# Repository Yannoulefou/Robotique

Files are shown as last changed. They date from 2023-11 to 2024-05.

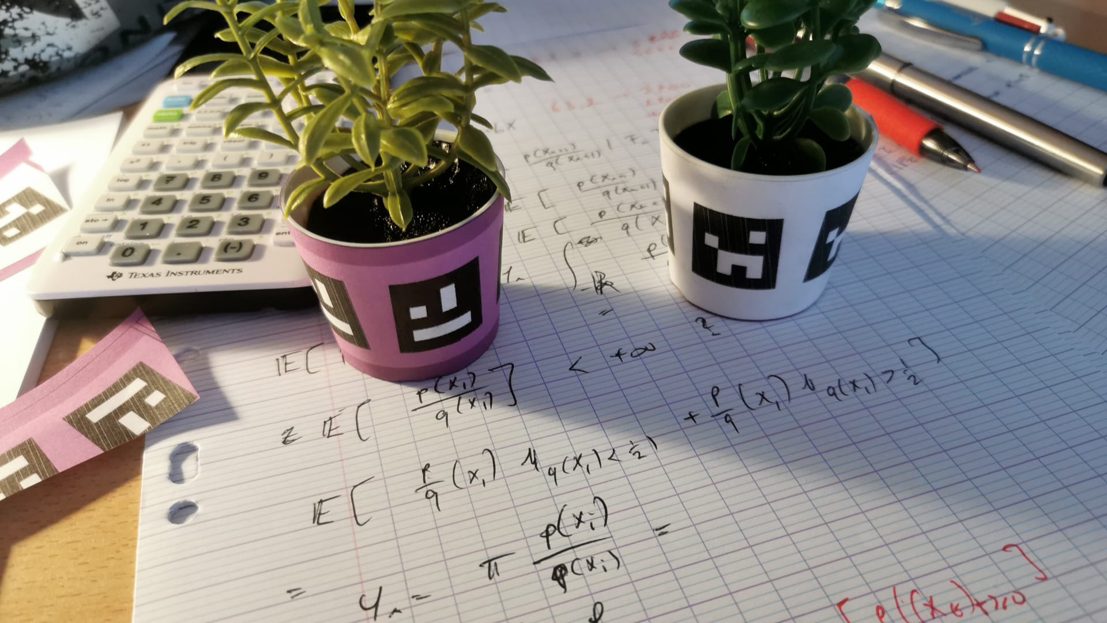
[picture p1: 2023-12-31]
Programmations/Tag Aruco/photo8.jpg

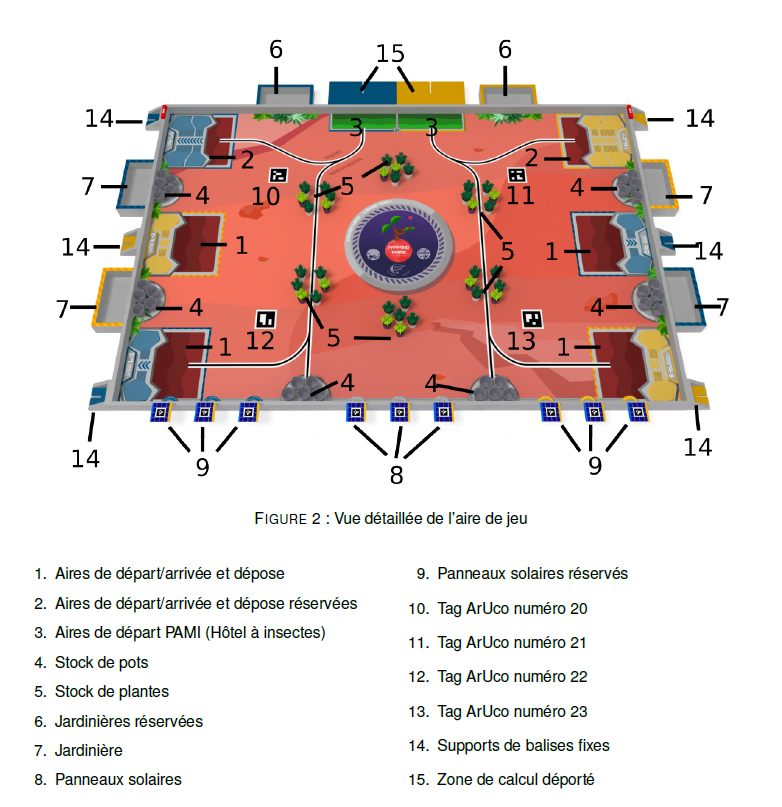
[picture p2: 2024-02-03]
Programmations/Moteur Deplacement/Schéma/Plateau.png

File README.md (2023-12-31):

# Robotique
Ce repo a pour but de centraliser tous les documents pour la participation à coupe de france de robotique 2023-2024 de TUXAE.  

## Sujet  
Farming Mars  
https://www.coupederobotique.fr/inscriptions-coupe-de-france-de-robotique-2024/  
https://www.eurobot.org/eurobot-contest/eurobot-2024/  

## Liens intéressants
https://github.com/VRAC-team/la-maxi-liste-ressources-eurobot  
https://github.com/LesKaribous   
https://howtomechatronics.com/projects/arduino-mecanum-wheels-robot/  
https://git.poivron-robotique.fr/Keuronde/Meca2024/src/branch/master   
https://mryslab.github.io/telemetrix/  

## Participants
### Conception Robot
 - Fanny DAUBET
 - Pierre DAUBET
 - Jacques ZHANG
 - Thomas CHEN
 - Tien-Thinh TRAN-THUONG (tttienthinh)

### Motorisation et roues omnidirectionnelles
 - Thomas ROUSSAUX

### Triangulation 
 - Victorien Marette  

### Caméra et computer Vision
 - Dasha HARYFULLINA ?

### Filtre de Kalman
 - Yassine BOUKHATEB (yassprogramme)
 - Mohamed KETEB
 - Guillot Paul (pyoph)

### Algorithme de décision (problème du sac à dos)
 - Wiam Lachqer ?
 - Bilal BENHANA ?
 - Rémy Siahaan-Gensollen ?

# Feuilles de route
## Novembre 2023
 - Apprendre à utiliser les machines (Imprimante 3D & Découpeuse Laser)
 - Réaliser des prototypes
 - Acheter les composants nécessaires
 - Lancer les différentes équipes

## Décembre 
 - Faire la demande de subvention pour l'association
 - Fixer un concept de robot
 - Réfléchir au cablage des composants et leur positionnement

## Janvier 2024
 - Commencer à intégrer les roues mecanum
 - Programmer le robot
 - Analyser l'algorithme de décision

## Février 
 - Commencer à intégrer la triangulation
 - Fabriquer les coccinelles
 - 10 février 2024 🏆 Rencontre Junior Auvergne-Rhône-Alpes 

## Mars
 - Commencer à intégrer les manoeuvres d'évitemment de l'adversaire
 - Commencer à intégrer une position plus précise par filtre de Kalman
 - 2 mars 2024 🏆 Rencontre Junior Ile-de-France 

## Avril 
 - 11 avril 2024 🏆 Eurobot Royaume-Uni 🇬🇧
 - 12 et 13 avril 2024 🏆 Eurobot et Eurobot Junior Espagne 🇪🇸
 - Rencontre à Télécom-Sud-Paris pour faire affronter les robots

## Mai
 - Du 8 au 11 mai 2024 🤖 Finales nationales et internationale 🤖

# Ressources

https://en.wikipedia.org/wiki/Python_Robotics  
https://arduinofactory.fr/pyfirmata/

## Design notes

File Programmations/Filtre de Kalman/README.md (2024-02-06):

# Les étapes
 - Comprendre le modèle 
 - Essayer de le mettre en place sur un modèle exemple : https://github.com/emmanuel-battesti/swarm-rescue/tree/main/src/swarm_rescue/examples
 - Essayer de comprendre les sources d'erreurs de la triangulation et les mesurer
 - Intégrer les erreurs pour l'estimation de la position

# Ressources
https://www.youtube.com/watch?v=IFeCIbljreY : Une vidéo très simple permettant de comprendre l'utilité du filtre de Kalman.

https://filterpy.readthedocs.io/en/latest/kalman/KalmanFilter.html : Un module python que j'ai déjà utilisé au sein d'un autre projet et que je trouve facile à prendre en main.

https://automaticaddison.com/extended-kalman-filter-ekf-with-python-code-example/ Une implémentation simple modèle #xt+1 = xt + v cos(theta)
#yt+1 = yt + v sin(theta) 
#theta_t+1 = theta_t + omega

https://atsushisakai.github.io/PythonRobotics/modules/slam/ekf_slam/ekf_slam.html#introduction Autre implémentation

https://github.com/rlabbe/Kalman-and-Bayesian-Filters-in-Python Des implémentations plus complexes ici

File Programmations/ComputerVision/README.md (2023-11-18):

# Les étapes
 - Lire un code barre dans une photo avec Python (1-lirecodebarre.py)
 - Essayer de dessiner soit même 3 code barres différents et les faire reconnaitre (1-lirecodebarre.py)
 - Identifier la position du Codebarre et son orientation (2-positioncodebarre.py)
 - Rendre la reconnaissance de code barre en temps réel et utiliser une caméra (3-webcam_live.py)
 - Faire en sorte que le temps réel ne prennent pas trop de ressources (3-webcam_live.py)
 - Basculer tout le code sur Raspberry avec la caméra intégré (4-Raspberry.py)
 - Faire la reconnaissance sur les poteaux de balises
 - Identifier la position de la balise et calculer la position en conséquence

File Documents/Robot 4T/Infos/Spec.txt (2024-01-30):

pyfirmata
https://github.com/MrYsLab/telemetrix
  
# Roue mecanum

Tbest Roue Omnidirectionnelle Mecan, Roue Omnidirectionnelle Mecanum en Alliage d'Aluminium de Robot RC avec Ecrous Dorés  
https://www.amazon.fr/Tbest-Omnidirectionnelle-Mecanum-Alliage-dAluminium/dp/B07YQJPFKW

Dimensions du produit (L x l x h) 	‎6 x 6 x 2,4 cm; 230 grammes 

Spécification:  
Condition: 100% tout neuf  
Type d'élément: Accessoire RC  
Matériau de la surface: alliage d'aluminium  
Couleur: comme sur les images  
Diamètre de roue: env.60mm/2.4in  
Modèle: 60mm  
Connecteur: env.12mm  
Roulement: 15 kg  
Épaisseur de roue: env.24mm  
Diamètre de l'essieu de la roue d'appui: env.4 mm  
Numéro de la roue de soutien: 10   

# Moteur NEMA

NEMA is an acronym for the National Electrical Manufacturers Association.  
NEMA 14 signifie que la face de devant fait 1.4*1.4 pouce = 3.5*3.5cm  
NEMA 17 signifie que la face de devant fait 1.7*1.7 pouce = 4.2*4.2cm  
La vitesse et le couple dépend donc de la longueur du moteur et de la puissance électrique acceptée.  

Différentes références de moteur NEMA :  
https://www.pololu.com/category/87/stepper-motors  

Exemple de NEMA 17
https://www.lextronic.fr/moteur-pas-a-pas-nema17-03-64826.html  

Sur omc-stepperonline.com   
Nema 23 série E bipolaire 1.8deg 1.26Nm 2.8A 57x57x56mm 4 fils €10.51    
Nema 17 Bipolaire 42Ncm  1.5A 42x42x38mm 4 Fils  €4.63  
Nema 17 Bipolaire 45Ncm 2A 42x42x40mm 4 Fils €7.69  
Nema 17 Bipolaire 59Ncm 2A 42x48mm 4 Fils €9.43   

# Moteur à encoder
333 rpm et 0.35 Nm  
https://www.lextronic.fr/motoreducteur-e52037gm-120333-76706.html  

# Batterie
[Comment alimenter la Raspberry](https://www.magdiblog.fr/divers/comment-alimenter-votre-raspberry-pi-avec-une-batterie/)  
Lipo : best mais dangeureuse lors de la charge  
Li ion : comme téléphone mais un peu chère  
Nimh (aka pile rechargeable) : Ok mais perd de puissance au cours de l'utilisation  

## melasta Li-ION Batterie Externe 5200mAh 12V/5A/DC 9V/1.5A/DC 5V/2A USB  
46,99€  
https://www.amazon.fr/Batterie-Portable-Compatible-Smartphone-Surveillance/dp/B0BRRR3C41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  
Power Bank Chargeur Portable avec Chargeur avec 3 Ports Sortie et 1 Entrées
Avec buton power off  

## Batterie Externe Power Bank 6000mAh 14.6V/5A/DC 9V/1.5A/DC 5V/2A USB   LiFePO4 
64,99€
https://www.amazon.fr/Batterie-Powerbank-Compatible-Smartphone-Surveillance/dp/B0BRTK7ZSD?ref_=ast_sto_dp  
Batterie Portable avec Chargeur avec 3 Ports USB Sortie et 1 Entrées  
Avec buton power off  

## Charmast 20000mAh 100W PD Batterie Externe Ordinateur Portable en USB C Batterie Portable Power Bank Quick Charge 3.0 
52,99€  
https://www.amazon.fr/Charmast-Ordinateur-Compatible-T%C3%A9l%C3%A9phone-Tablettes/dp/B0C1N9D7S9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
100W = 5A * 20V ?  
Avec buton power off  

## Power Bank 20000mah,PD 100 W,Power Bank 5A à Charge Rapide,Ports D'EntréE et de Sortie USB C,BoîTier Translucide,Affichage NuméRique
49.99€
https://www.amazon.fr/20000mah-DEntr%C3%A9E-Translucide-Affichage-Num%C3%A9Rique/dp/B0CG1FRC19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

## USB Cable Y Splitter USB 2.0 Power Enhancer Hub Adapter Data Charger Cable Extension Code Type a 30cm (1 Female to 2 Male)    
7.99€
https://www.amazon.com/Splitter-Enhancer-Adapter-Charger-Extension/dp/B072LLMKJF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

## USB 3.0 Hub, VIENON 4-Port USB Hub USB Splitter USB Expander for Laptop, Xbox, Flash Drive, HDD, Console, Printer, Camera,Keyborad, Mouse 
7.99€
https://www.amazon.com/Extender-Splitter-MacBook-Chromebook-Pixelbook/dp/B09MLRPTT2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

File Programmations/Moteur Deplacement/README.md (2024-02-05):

Salut Yassine,

Tu trouveras dans le dossier https://github.com/Tuxae/Robotique/tree/main/Programmations/Moteur%20Deplacement tous les fichiers dont tu auras besoin.

On a réussi à faire tourner les moteurs pas à pas (des moteurs très précis : https://www.youtube.com/watch?v=fQsdUhRwCU4) 

Est ce que tu pourrais : 
 - Compléter la méthode BaseDiffCalcul.calculer_position dans le fichier BaseDiff.py pour connaitre la position relative du robot à tout instant stp ?
 - Compléter la liste d'action dans main.py pour que le robot suive le chemin dessiné dans Schéma_deplacement stp (si possible pour faire des tests ce lundi) ?

Je pense que ça pourrait être une superbe idée de commencer par faire une fonction pos2actions qui prend en entrée la position et angle initiale et finale voulue et qui donne en sortie la liste d'action à réaliser. J'ai l'impression que des librairies existent déjà dans ce domaine tu peux carrément les utiliser.

Je t'ai mis des documents dans Schéma, mais si besoin tu peux te référrer à Documents\Présentation\Eurobot2024_Rules_CUP_FR_FINAL.pdf pour plus d'info ou me demander.

En tout cas, merci beaucoup pour ton aide Yassine, j'espère que ça va te plaire de participer !

Tien-Thinh

# Ressources intéressantes
https://classes.engineering.wustl.edu/cse550/a01.php  
https://atsushisakai.github.io/PythonRobotics/modules/control/move_to_a_pose_control/move_to_a_pose_control.html  
https://github.com/VRAC-team/la-maxi-liste-ressources-eurobot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

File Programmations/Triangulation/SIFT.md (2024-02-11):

On pourrait faire de l'odométrie ou de la triangulation en utilisant SIFT

https://makina-corpus.com/data-science/utilisation-de-la-vision-par-ordinateur-pour-redresser-des-images

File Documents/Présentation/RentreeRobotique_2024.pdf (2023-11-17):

# Présentation règlement 2024

## ECE Paris

09/09/23

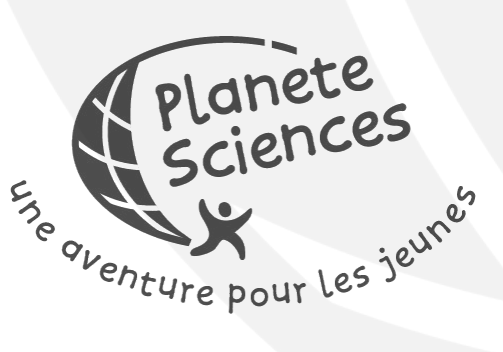
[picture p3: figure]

# La commission règlement

Merci aux astronautes 2024 :

- Sullivan
- Florence
- Corentin
- Tony
- Rémi
- Rémy
- Baptiste
- Jonathan
- Christophe
- Hugo
- Camille
- Hendrick

# Les documents

Règlement très similaire pour les concours Eurobot et Eurobot Junior.

Mais 2 documents différents !

Le but est d’alléger les règlements en ne mélangeant pas les cas particuliers propres à chaque concours

# Les matchs

- 2 équipes se rencontrent
- 3 minutes de préparation sur l’aire de jeu
- 100 secondes de match
- Interdiction d’intervenir
- Victoire, égalité, défaite : 1 point
- Forfait : 0 point
- Pénalités : selon le cas

# Avant propos

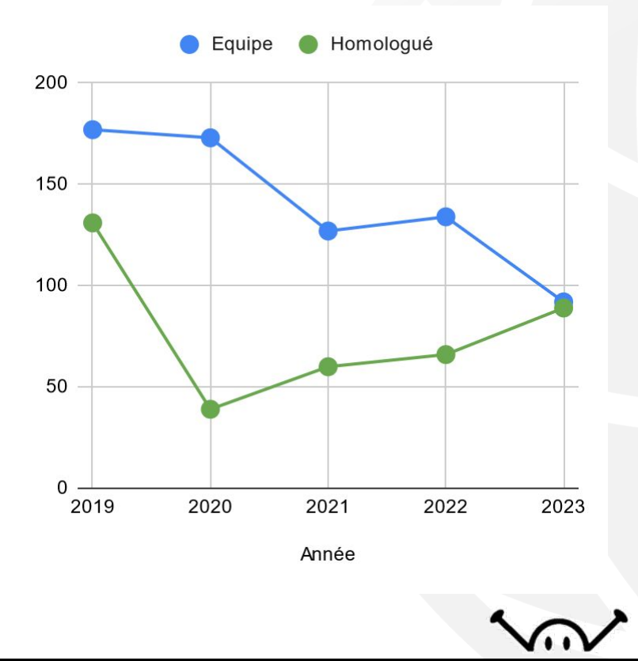
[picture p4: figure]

La remontée du niveau des équipes

- Même si le nombre d’équipes continue de baisser, le nombre d’homologation est bien remonté
- Une bonne base d’équipes avec des bases roulantes
fonctionnelles, on peut remonter le niveau de la coupe

- Passage à 1 robot
- Remise en place d’action plus complexe : juste pousser ne rapporte qu’une fraction des points (environ ⅓ de l’action principale)
- Retour à une orientation de table traditionnelle (tout en largeur)
- Elément de jeu imprimé en 3D
- Ajout des PAMI (Petit Automate Motorisé Indépendant) et aide au calcul.

Changement de stratégie pour le règlement 2024 :

# Le thème 2024 est

# LA CULTURE SUR MARS

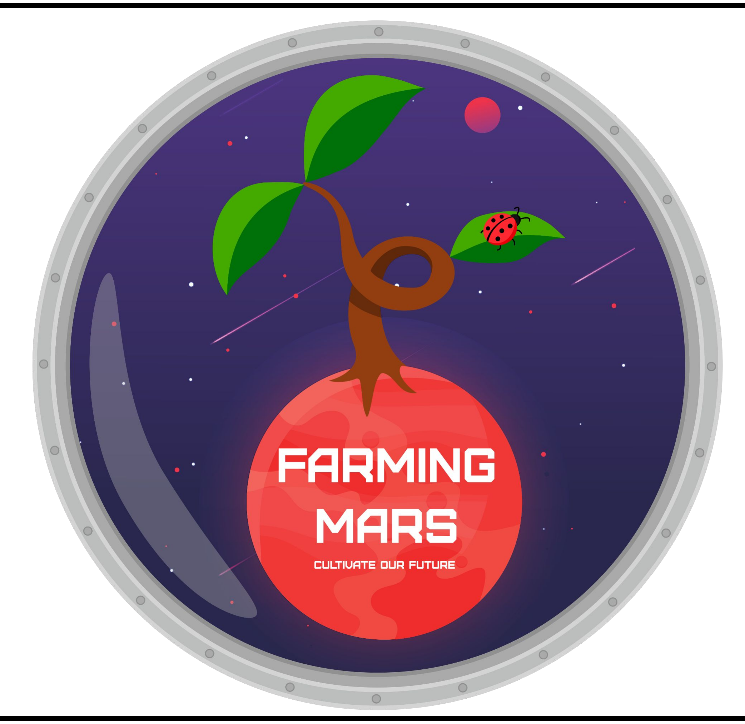
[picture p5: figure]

# Un petit peu d’histoire

Espace, frontière de l’infini vers laquelle voyage notre vaisseau spatial, notre première étape : Mars.

Mais si on arrive à l’heure du déjeuner, comment allons nous nous sustenter ? Les gâteaux de mémère Monique ayant tous été mangés l’an dernier !

C’est pourquoi nos robots ont une mission très importante pour la bonne réussite de notre voyage : préparer le terrain et faire des réserves de nourriture ! Ou plus exactement, faire en sorte que la serre autonome déjà mis en place survive assez longtemps pour que nos astronautes puissent récolter des fruits et légumes, et ainsi survivre !

# L’aire de jeu

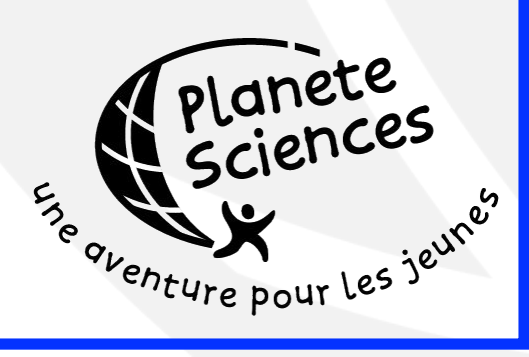
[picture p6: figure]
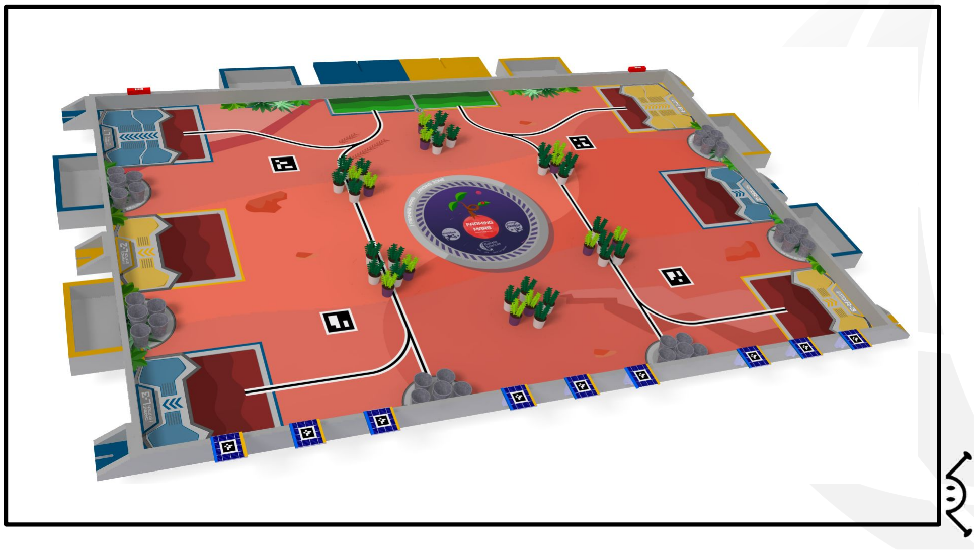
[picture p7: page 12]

Rajouter la table

# L’aire de jeu

- Dimensions de la table : 2 000 x 3 000 mm
- Hauteur de la bordure : 70 mm
- Pour les Coupes Junior et Eurobot Junior
- Pas de support de balises latérales ou zone de calcul, mais tag de couleur pour distinguer les robots.
- Pour la Coupe de France de Robotique et Eurobot
- Balises fixes : dispositif conservé (avec un nouveau modèle)
- Nouveau dispositif : Zone de calcul déporté

# La zone de calcul déporté

- Remplace le mât central, en position centrale à l’arrière de la table
- Réutilise le “support de panier”
- Dimensions de la zone: 45 x 32 cm x 160 cm de haut, 5kg max
- Permet d’avoir un système de calcul indépendant, plus puissant et déporté qui peut communiquer avec le robot, les PAMI et les balises.
- Permet de faire du repérage sur la table (comme l’ancien système de mât central)
- Attention à la communication, à l’encombrement et à la fixation (tige filetée M8 et écrou papillon).

# But du jeu

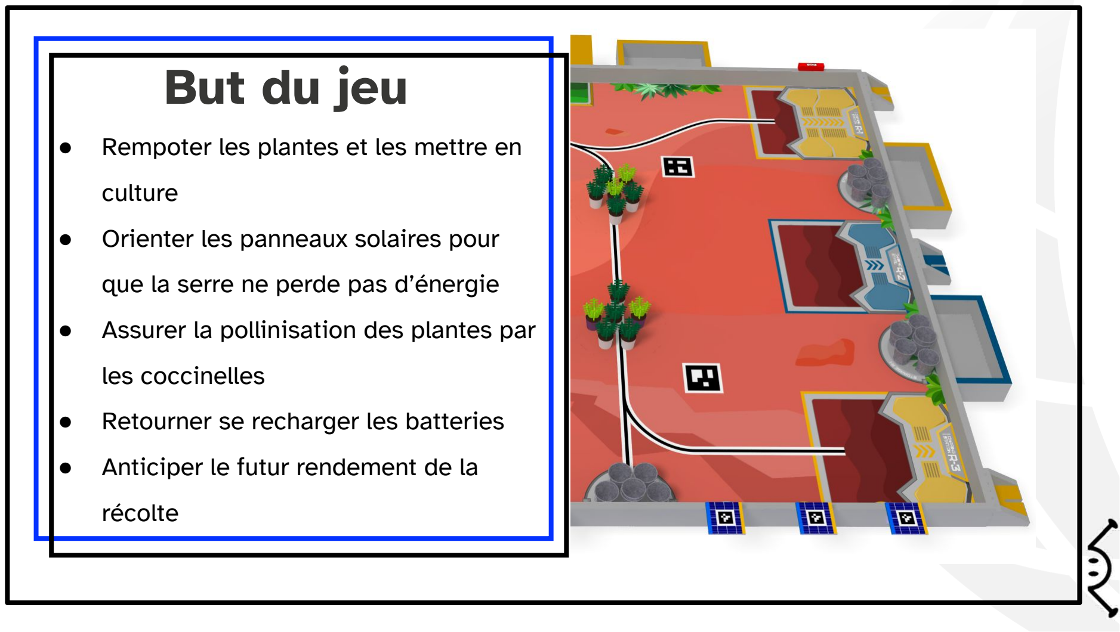
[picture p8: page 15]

- Rempoter les plantes et les mettre en culture
- Orienter les panneaux solaires pour que la serre ne perde pas d’énergie
- Assurer la pollinisation des plantes par les coccinelles
- Retourner se recharger les batteries
- Anticiper le futur rendement de la récolte

rajouter image table

# Rempoter les plantes et les mettre en culture

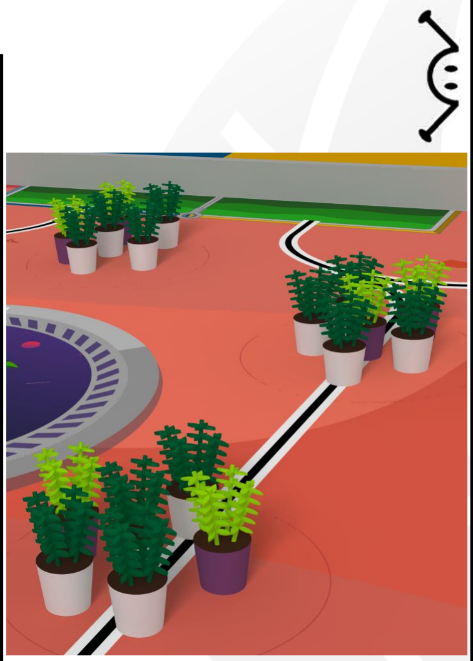
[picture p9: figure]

# L’objectif

Les robots doivent ramasser les plantes, les mettre dans les pots et les disposer dans une zone de culture adaptée, avec une limite de 6 plantes par zone de culture.

## Les Plantes

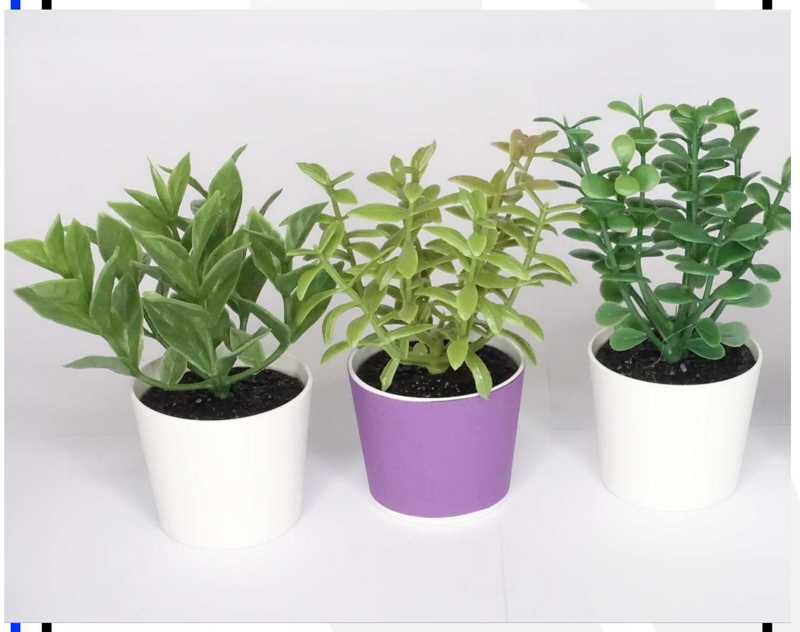
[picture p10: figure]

- Plante en plastique de (chut chut, pas de marque !)
- Dimensions: 5 cm de diamètre et de 10 cm de haut
- base blanche ou violette
- tag RFID placé en-dessous

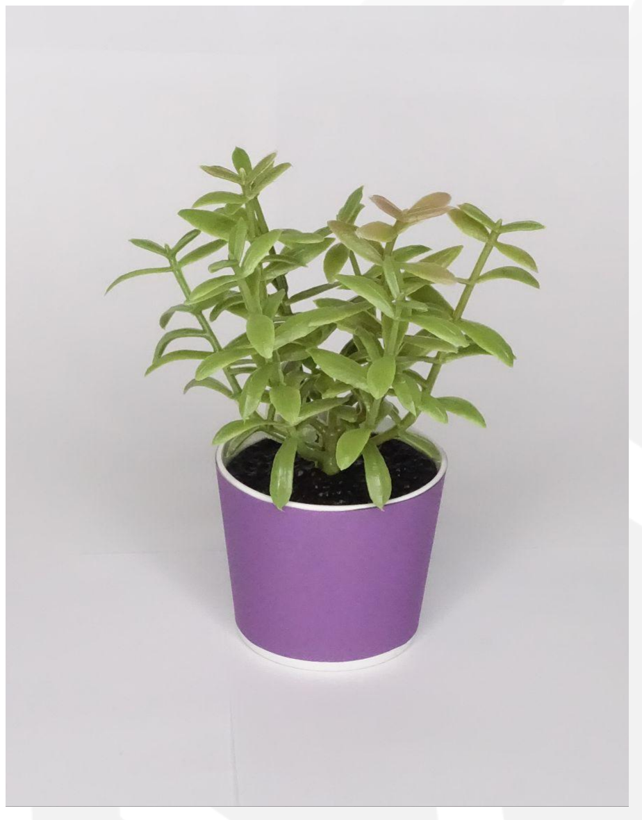
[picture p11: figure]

# Les Plantes

2 types de plante :
1. Résistante (base violette, tag RFID 2) : supporte tous les environnements,
12 sur la table.
2. Fragile (base blanche, tag RFID 1) : supporte seulement les jardinières, 24 sur la table.

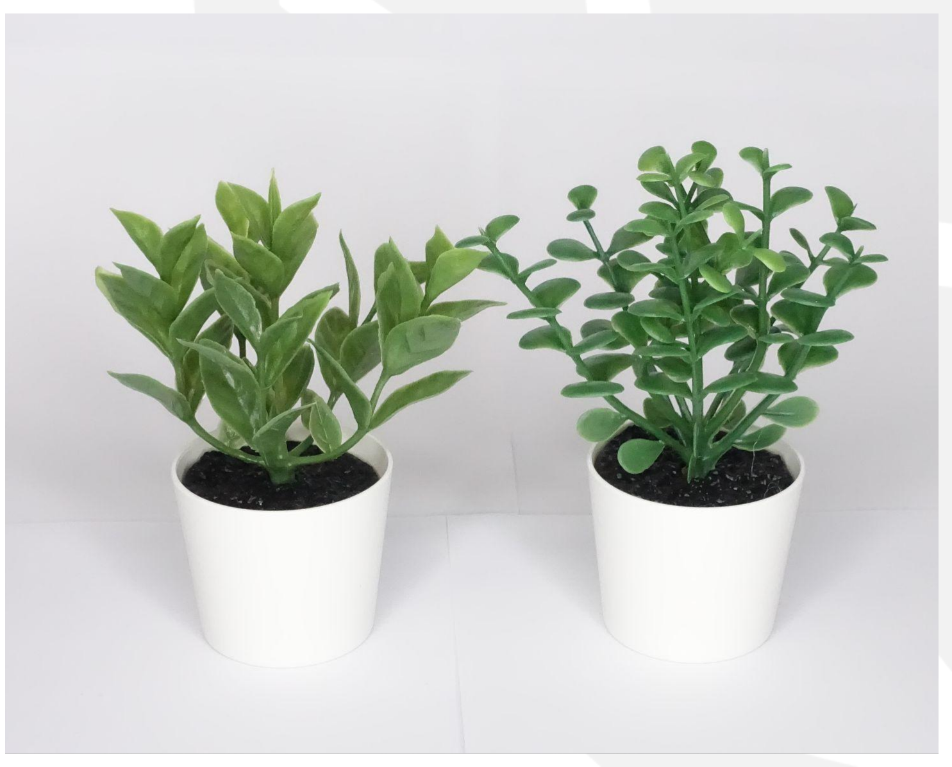
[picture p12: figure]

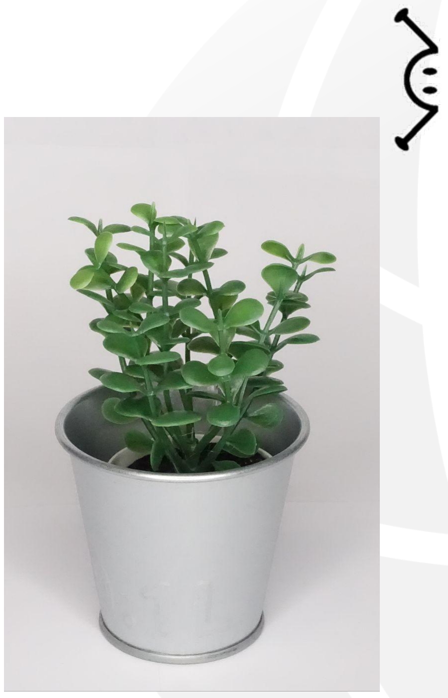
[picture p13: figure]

## Les Pots

- Pot en fer (chut chut, pas de marque!)
- Dimensions: 7 cm de diamètre et de 7 cm de haut (contenant de 0.1L)
- Doit contenir une plante en fin de match

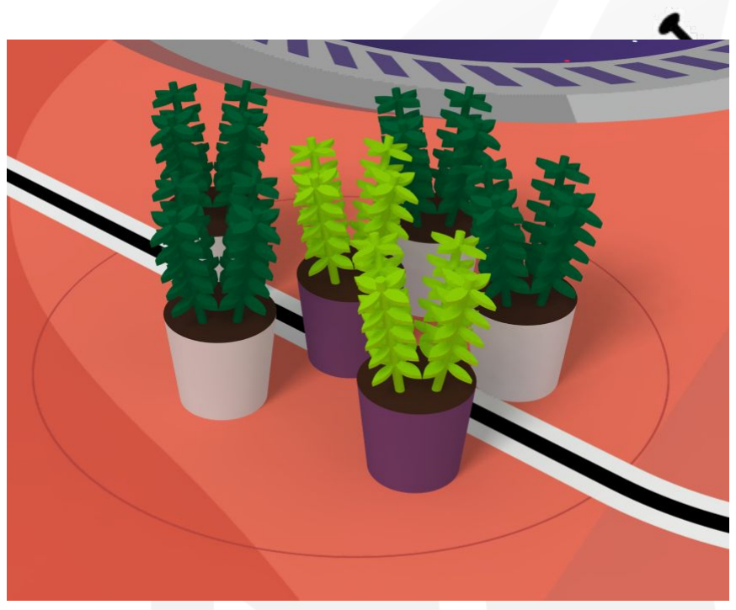
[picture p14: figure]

## Les plantes

- 6 zones ronde de 30 cm au centre de la table
- 6 par zone (2 résistantes et 4 fragiles disposées au hasard dans la zone)

## Les pots

- 6 zones en demi-cercle de 25 cm sur les côtés et le devant de la table
- 6 par zone dont deux empilés au centre

## Dispositions initiales

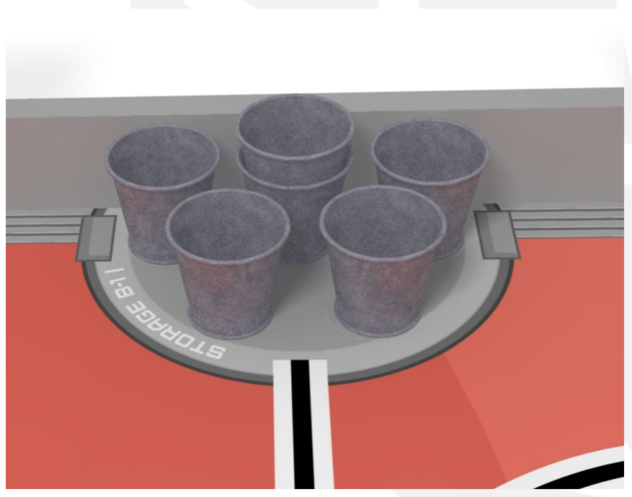
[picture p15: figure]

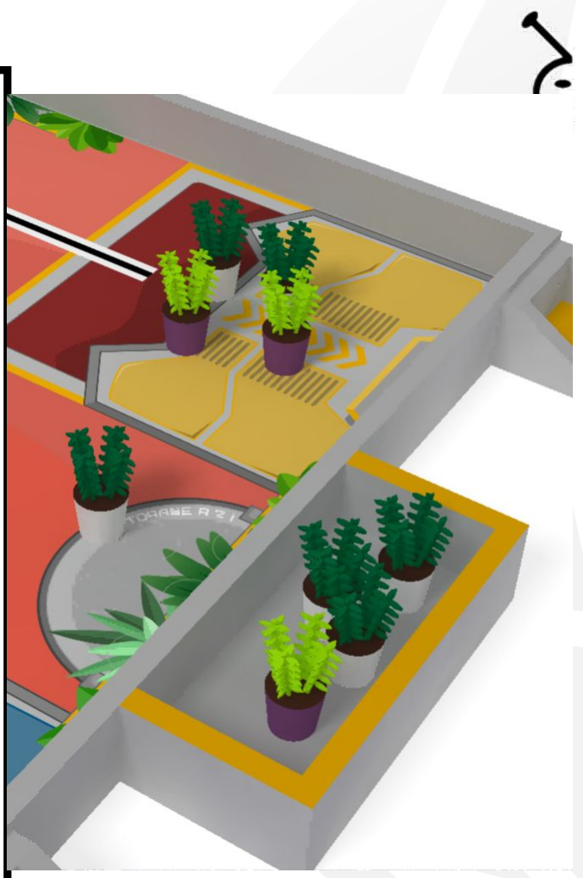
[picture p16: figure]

## Zones de dépose

## Les parterres

- Zones carrées de 45 cm de côté sur les bords de la table
- 1 protégée, 2 volables par équipe

## Les jardinières

- Support externe à la table de 32,5 cm de large, sur les bords de la table
- 2 protégées, 1 volable par équipe

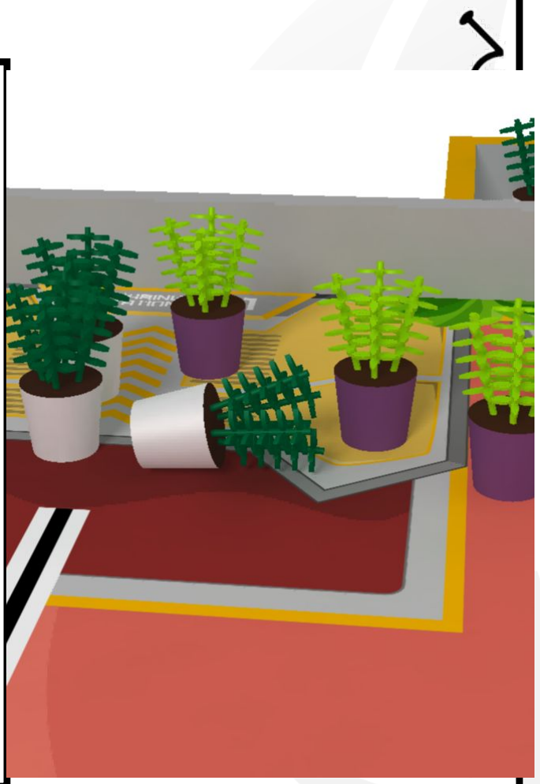
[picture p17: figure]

# Validité des plantes

- Tout ou partie de la surface de contact entre le sol et sa base ou son pot dans une zone adaptée.
- Restée debout
- 6 plantes par zone comptabilisées à l’avantage de l’équipe
- Non contrôlée par le robot en fin de match

# Points : Plante et pot

- ? points par plante valide dans une zone adaptée
- ? points supplémentaires si la plante valide est dans un pot

# Orienter les panneaux solaires

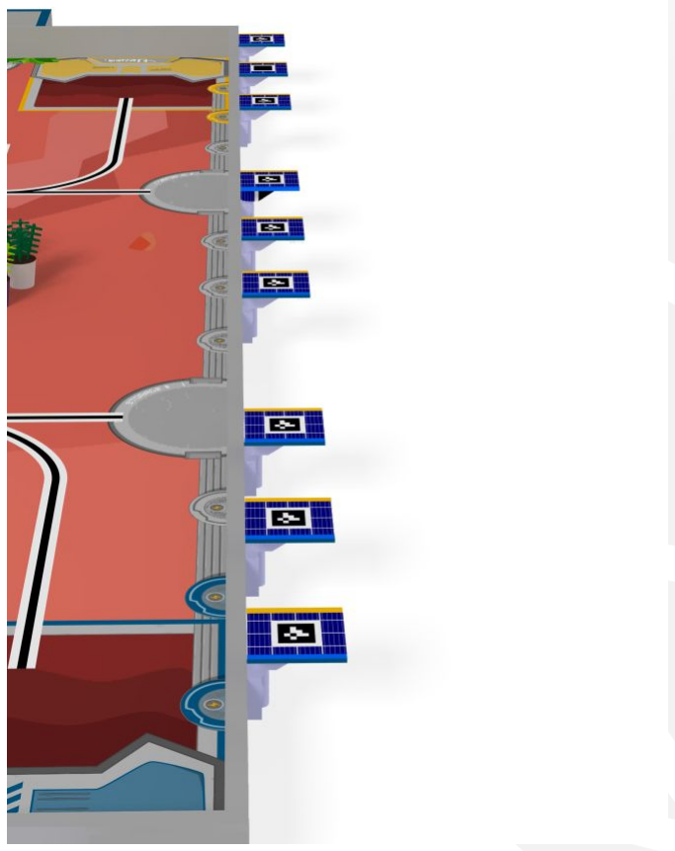
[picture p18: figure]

# Les Panneaux solaires

- Elément de jeu imprimé en 3D, avec un vinyle comprenant 2 bandes latérales de couleur
- 1 Elément mobile
- Placé sur le devant de la table
- Total de 9, dont 4 réservés aux équipes (2 pour chaque)

# Objectif

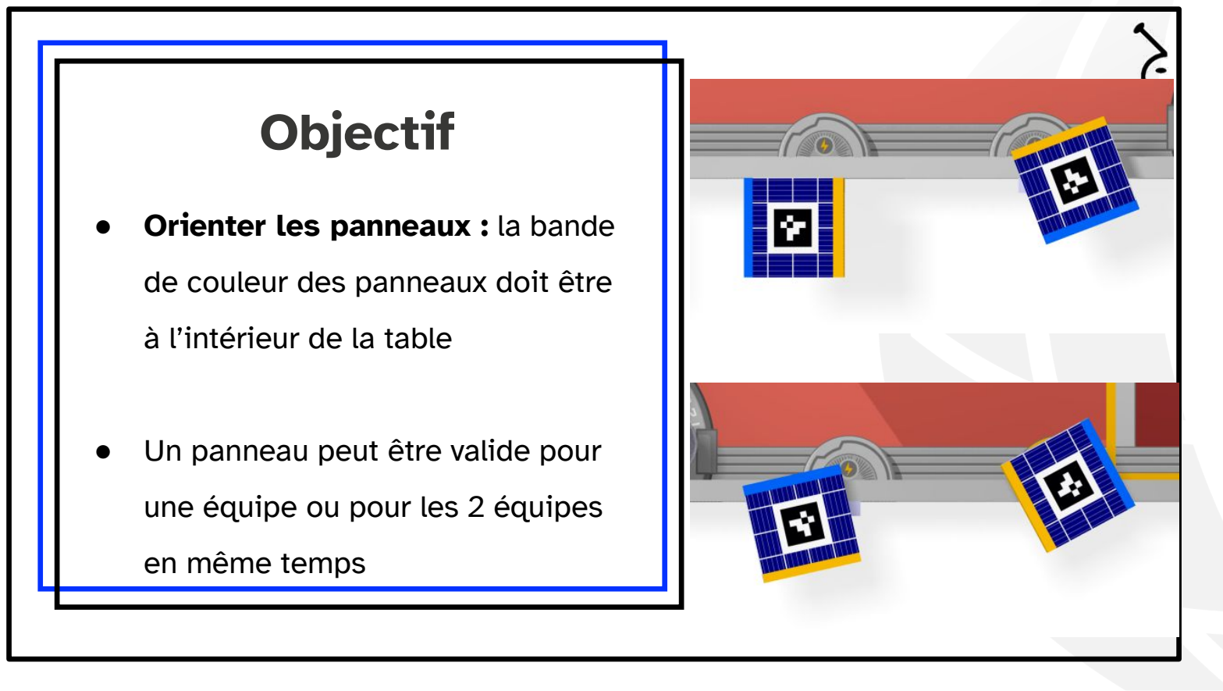
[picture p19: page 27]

- Orienter les panneaux : la bande de couleur des panneaux doit être à l’intérieur de la table
- Un panneau peut être valide pour une équipe ou pour les 2 équipes en même temps

# Points : Panneau

- ? points pour chaque panneau valide pour l'équipe

# Assurer la pollinisation des plantes

# Les coccinelles

- Les coccinelles (PAMI) sont fabriquées par les équipes
- Disposée dans la zone de départ des PAMI avant le match
- Doit sortir de la zone de départ entre la 90eme et la 100eme seconde de match
- A 10 seconde pour aller toucher une plante ou un pot contenant la plante dans une zone de dépose
- En fin de match : doit rester en contact de la plante

# Une coccinelle

- Peut :
- Être touchée par le robot de son équipe, mais pas manipulée
- Ne peut pas :
- Amener une plante dans une zone
- Sortir une plante d’une zone
(Invalidation de l’action de la coccinelle le cas échéant)

Le PAMI (Petit Automate Motorisé Indépendant)

- Doit respecter les mêmes contraintes de conception que les robots (BAU, évitement, laser, sac pour batterie lipo,...)
- Peut se déployer dans la limite d’une augmentation de 10 cm de son périmètre
- Est exempt de :
- mat de balise.
- support de balise (et donc pas de marqueur ArUco).

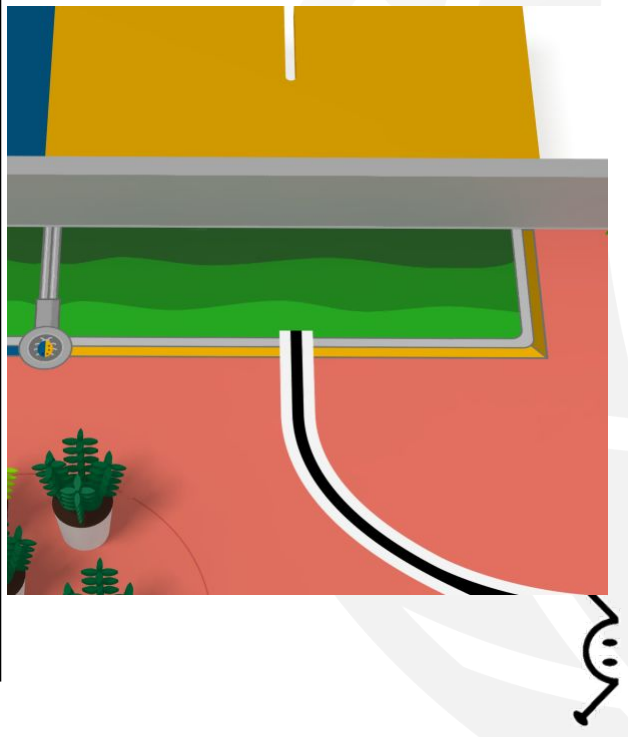
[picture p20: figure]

# Dimension du PAMI

- Dimension :
- minimum : un cube de 6cm de côté
- 15 cm de haut max
- l’ensemble des PAMI doit entrer dans la zone de départ des PAMI: 45 x 15 cm

# Limite des PAMI

- Quantité ≥ 0
- Non empilable
- 1kg max
- Autonome (même pour les Juniors)

# Points : Coccinelle

- ? points par zone de dépose de l'équipe occupée par au moins une coccinelle à la fin du match
- ? points supplémentaires par la zone de dépose de l'équipe dans laquelle au moins une coccinelle est en contact avec une plante ou un pot contenant une plante en fin de match
- Attention : si une coccinelle réalise ses actions dans une zone adverse, alors les points ainsi fait vont à l'équipe adverse

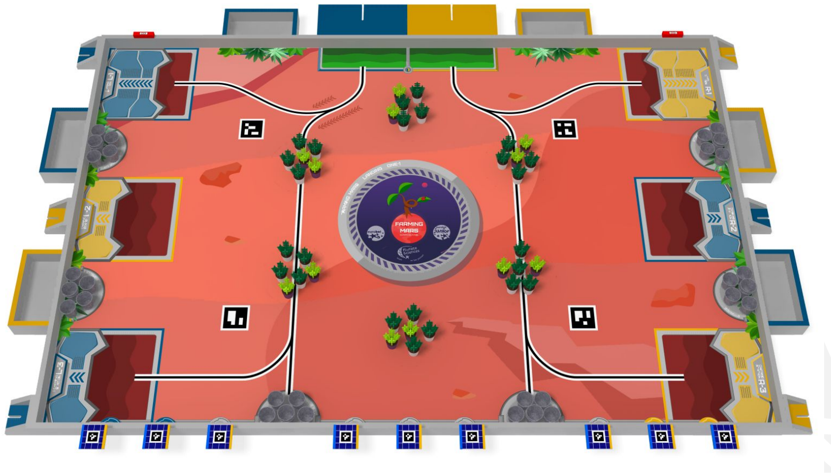
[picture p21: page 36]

Retourner se recharger les batteries,

# à la fin de la journée de travail

# À la fin de la journée de travail

- Objectif : finir le match dans l’une des zones qui a encore de la batterie, une zone différente de la zone de départ (celle avec le tag)

# En début de journée de travail

- Zones de départ : parterre de dépose de plantes sur les bords de la table, 45 cm x 45 cm.
- Les arbitres mettront un tag pour marquer la zone de départ du robot.

# Points : retour dans les zones

- 15 points si tous les robots de l'équipe sont dans la même
| zone
Cas Eurobot Junior :
- 15 points si le robot principal finit dans une zone.

Cas Eurobot :

# Points : retour dans les zones

- ? points si le robot de l'équipe est dans une aire de recharge valide

# Anticiper le futur rendement de la

récolte.

Points : rendement.

L’estimation se base les actions suivantes:
- REMPOTER LES PLANTES ET LES METTRE EN CULTURE.
- ORIENTER LES PANNEAUX SOLAIRES.
- RETOURNER SE RECHARGER LES BATTERIES

méthode de calcul :
Bonus = ? - |Score du match - Score Estimé|

# LES POINTS !!!

# Pas de points… pour l’instant

La version bêta du règlement sort sans les points. Rassurez-vous un équilibrage est déjà fait, mais on souhaite connaître vos équilibrage afin d’obtenir le meilleur équilibrage possible. (Intelligence collective, tout ça…)

A vos calculs!

# Règle d'équilibrage

- Partir sur une base de 1 ou 2 points pour l’action la plus simple,
- Toujours avoir un nombre de point entier,
- Eviter les équilibrages égoïstes où seules les actions que vous êtes capable de réaliser ont des points,
- Penser à toutes les équipes, des plus expérimentées aux débutantes, afin que tout le monde puisse marquer des points et ne pas repartir frustré de la rencontre,
- Autant de possible, avoir un équilibrage qui facilite le comptage des points (ex : total pour un gâteau + tri + cerise = 10pts),
- Une seule réponse par équipe, nous sélectionnerons la plus récente en cas de réponses multiples.

# Comment faire?

Vous avez jusqu’au 09 octobre pour répondre au formulaire, après quoi nous analyserons vos réponses et pondérerons l’équilibrage prévu en fonction de vos réponses, et pour cela il faut se rendre à l’adresse suivante et remplir le formulaire en ligne : www.eurobot.org/proposition_equilibrage (or www.eurobot.org/balancing_proposal in english)

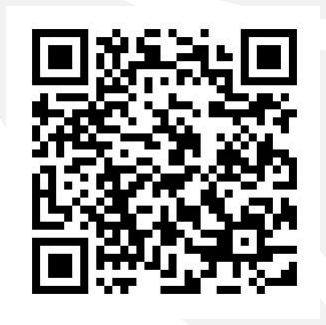
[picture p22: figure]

Nous publierons l’équilibrage avec la version finale du règlement.

# Avant de finir

# Les légendes

## On continue!

Même règlement, mais ……
Ouverture à tout le monde, même les eurobots avec 2 robots par équipe sur la table et les contraintes habituelles.

# Changement dans la partie fixe du règlement

- PAMI
- Calcul déporté
- Tag pour les juniors
- Autorisation des bases commerciales, si elles sont significativement modifiées
- un truc que vous trouverez vous-même en relisant attentivement le règlement de la page 1 à la page 46 #BAU

# Non-conformité lors des rencontres

Il ne sera pas possible de contester des points du règlement lors des rencontres. (À vous de lire le règlement dans son intégralité).

Si vous souhaitez demander une autorisation spéciale pour un cas particulier, merci de contacter l’organisation avant la rencontre.

# Outils

- Pour poser une question aux arbitres ou sur le concours

eurobot.org/faq

- Pour trouver des ressources

eurobot.org/wiki

- Pour échanger avec les équipes

Discord autogéré
https://discord.gg/tteC3Cp

# Le calendrier

- 09 septembre 2023 : Mise en ligne du règlement (version Bêta)
- 7 octobre 2023 : Questions-réponses sur les ondes (en stream)
- 9 octobre 2023 à 19h59m42s : Fin de la consultation sur la FAQ
Planète | Sciences | et | fin | proposition | d’équilibrage
- 15 octobre 2023 : Publication du règlement en version finale

# Merci de votre attention

# À bientôt à la Coupe !

# Des questions ?

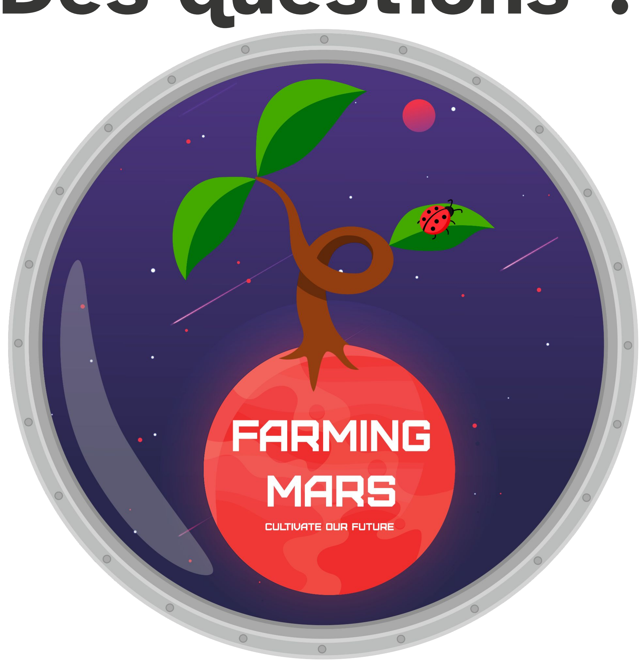
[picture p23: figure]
Rajouter la table
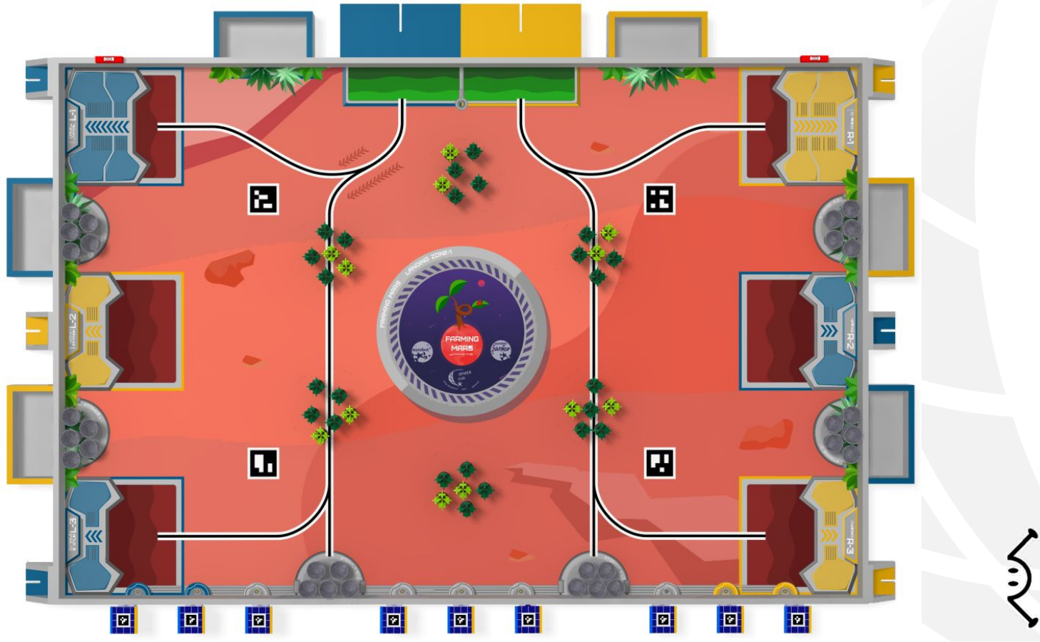
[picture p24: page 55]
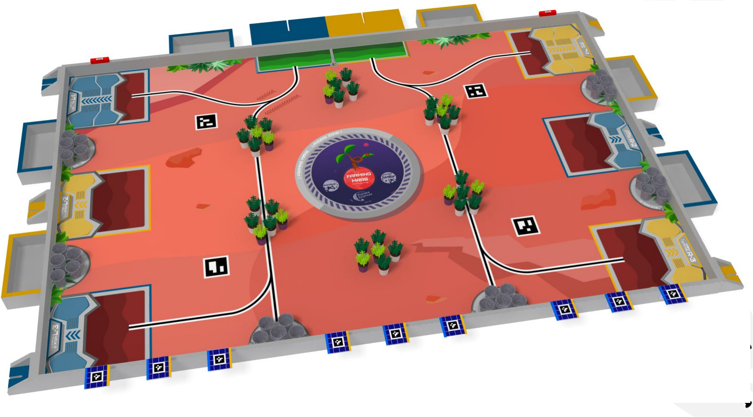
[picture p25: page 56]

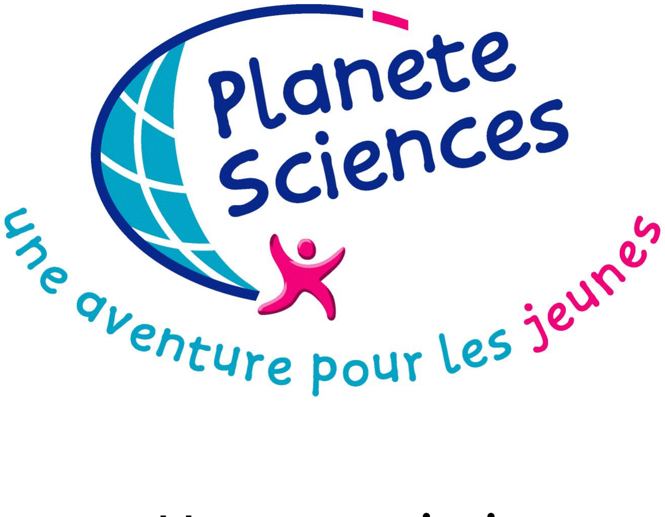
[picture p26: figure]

Une association
WWW.PLANETE-SCIENCES.ORG

10 Rue du Marquis de Raies, 91080 EVRY-COURCOURONNES / 01 69 02 76 10

## referee@planete-sciences.org


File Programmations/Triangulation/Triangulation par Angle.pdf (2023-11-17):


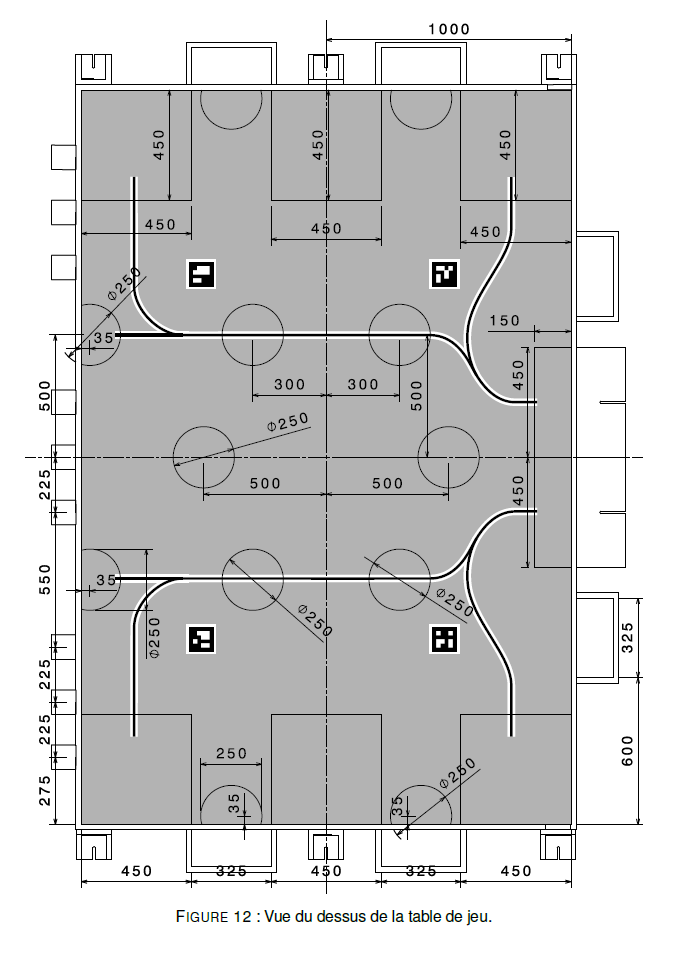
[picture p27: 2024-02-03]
Programmations/Moteur Deplacement/Schéma/Dimension Plateau.png

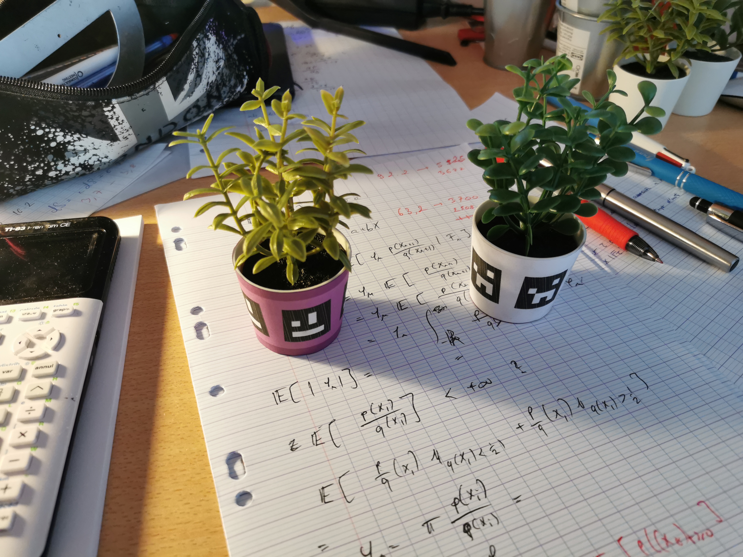
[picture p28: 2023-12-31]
Programmations/Tag Aruco/photo.jpg

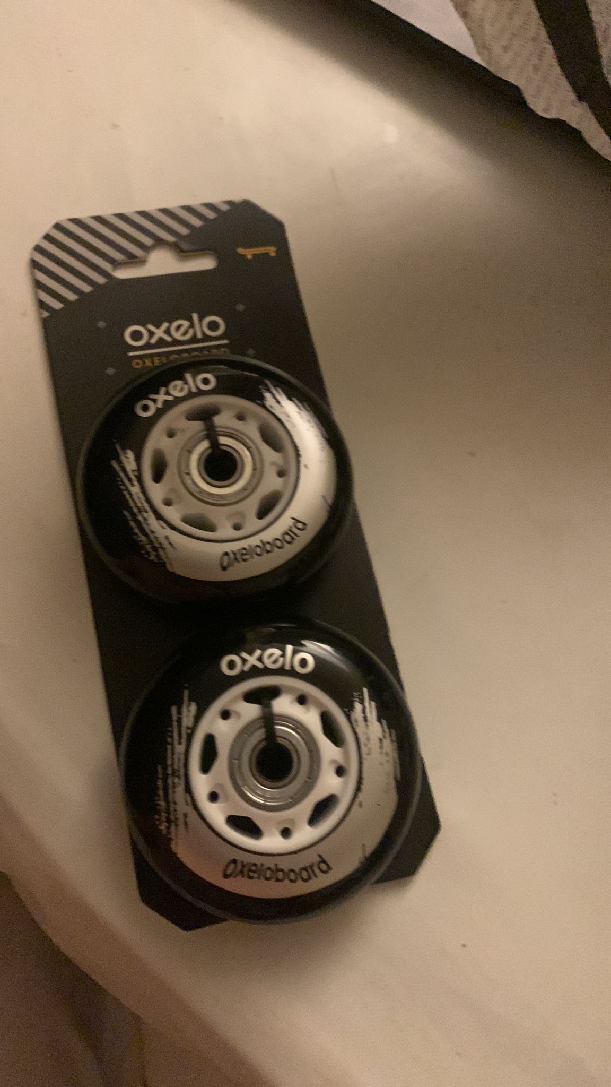
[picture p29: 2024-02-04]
Programmations/Moteur Deplacement/Schéma/Roue.jpg

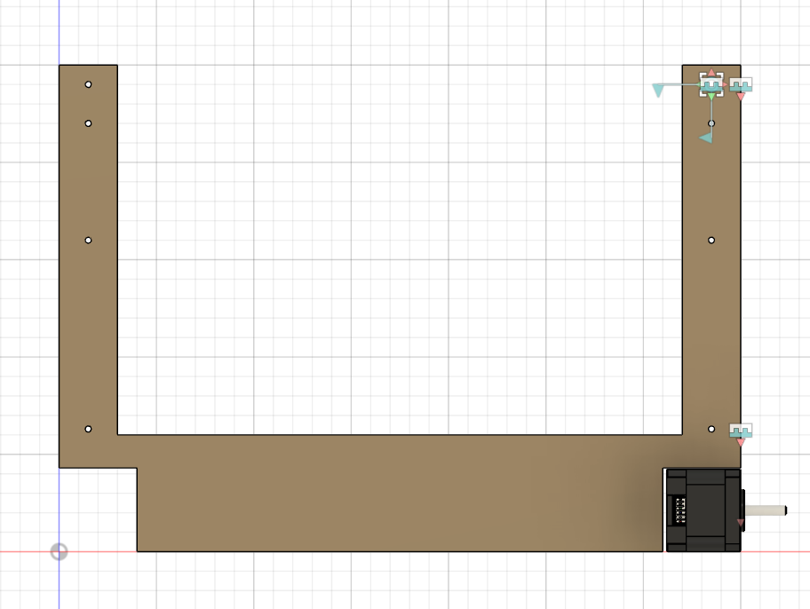
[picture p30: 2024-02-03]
Programmations/Moteur Deplacement/Schéma/Base Moteur.png

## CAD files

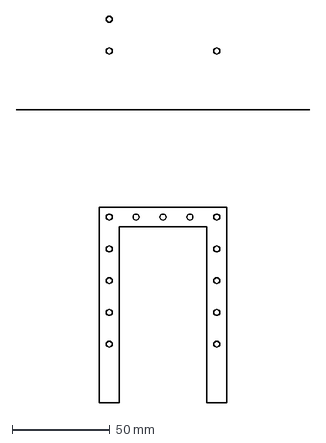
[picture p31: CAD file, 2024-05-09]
Decoupe/Maintien.dxf
150.0 x 197.8 mm

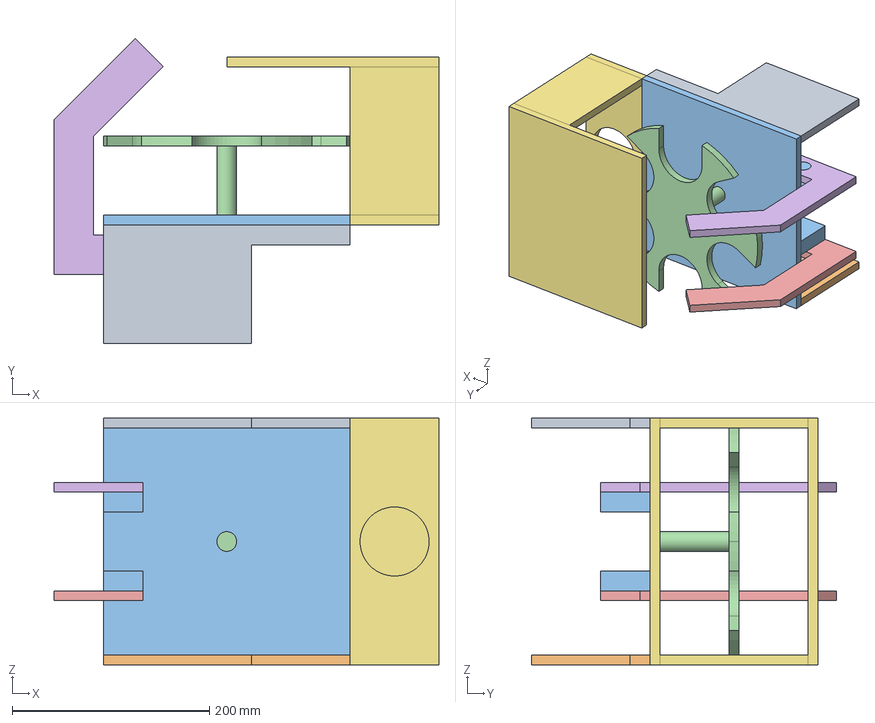
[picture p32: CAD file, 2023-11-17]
Documents/Robot 4T/Assemblage/Assemblage.FCStd
390.0 x 309.0 x 250.0 mm
Cote_001
Cote_002
Haut_001
Plateau_001
Pince_001
Pince_002
Arriere_001

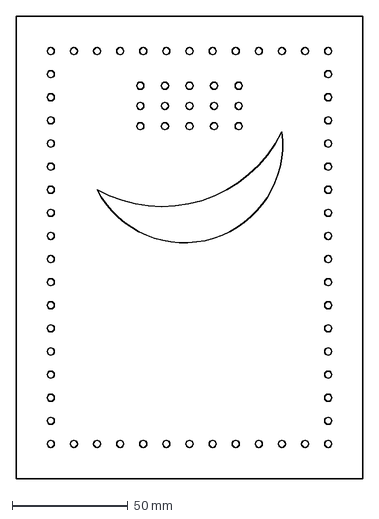
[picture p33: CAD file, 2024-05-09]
Decoupe/Devant.dxf
150.0 x 200.0 mm

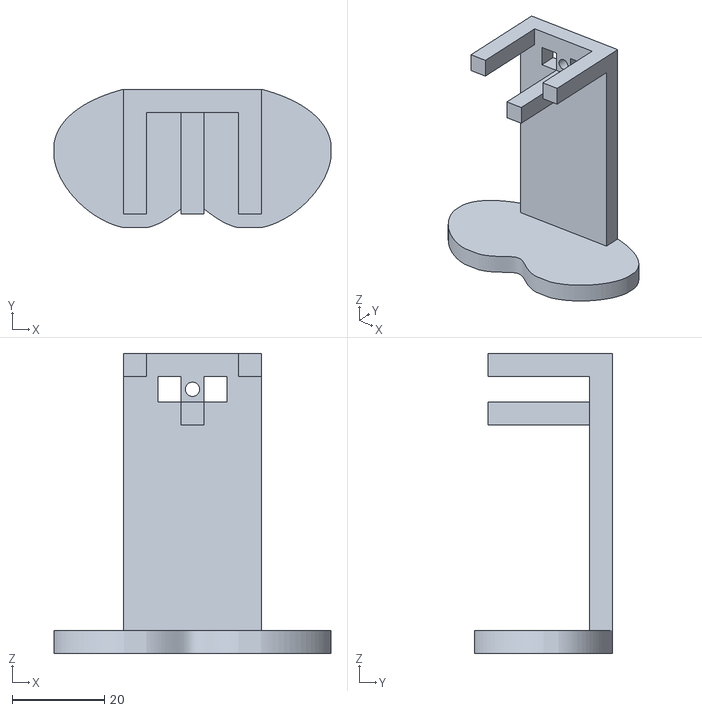
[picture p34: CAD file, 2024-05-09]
Decoupe/Pami/Lunette Pami.stl
60.0 x 30.0 x 65.0

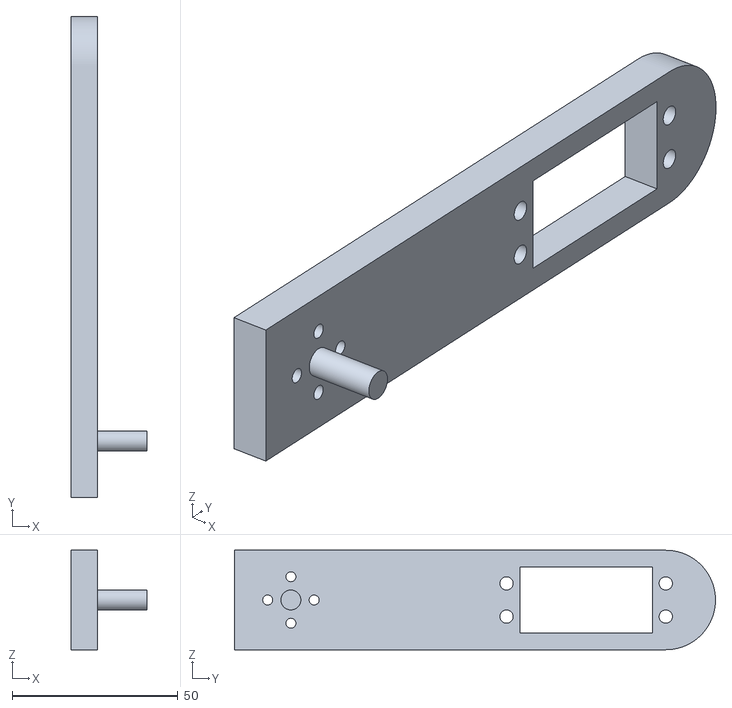
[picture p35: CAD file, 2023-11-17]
Documents/Fichiers 3D Eurobot/Bras.obj
23.0 x 145.0 x 30.0

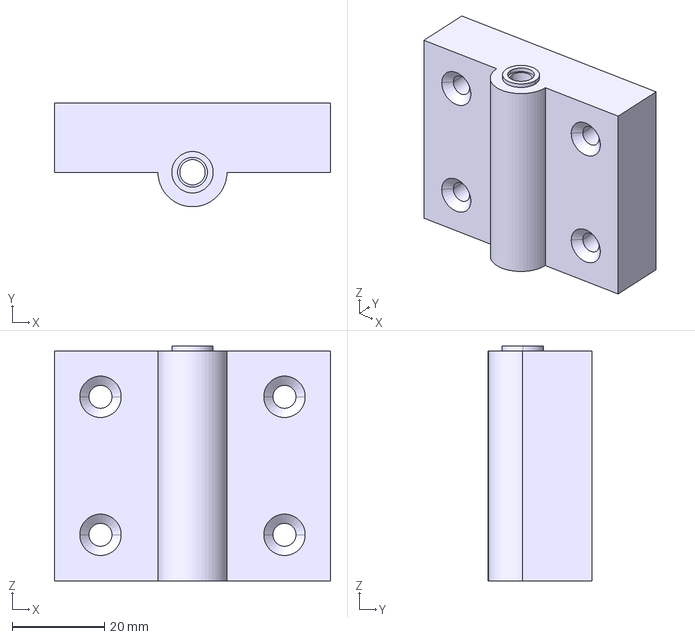
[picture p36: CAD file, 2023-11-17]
Documents/Matériel/3D_2024_BETA/step/support_panneau.stp
60.0 x 22.5 x 51.0 mm

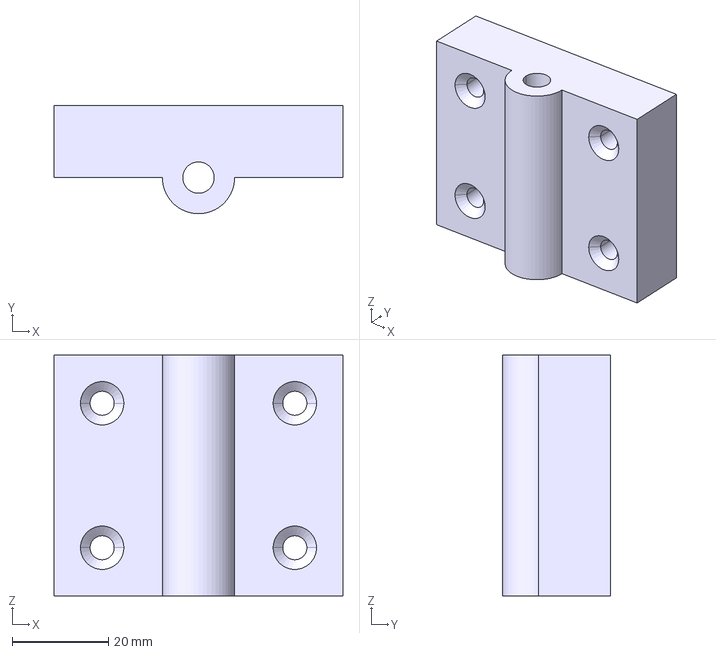
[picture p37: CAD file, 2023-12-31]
Documents/Matériel/3D_FINALE_V1/step/Support Panneau Solaire.stp
60.0 x 22.5 x 50.0 mm

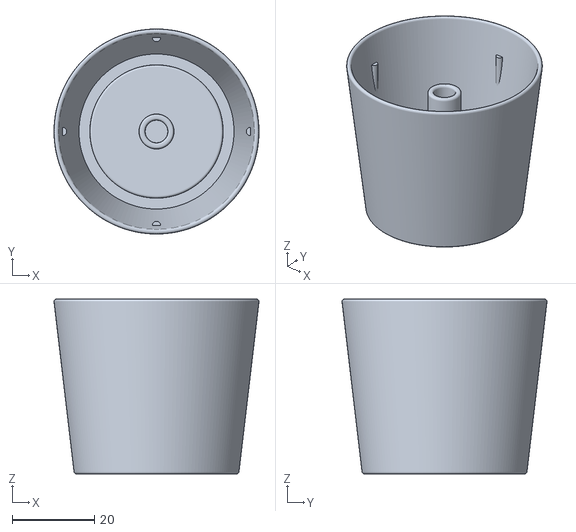
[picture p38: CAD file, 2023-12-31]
Documents/Matériel/stl_FINALE_V1/Pot_Plante.stl
49.9 x 49.9 x 42.5

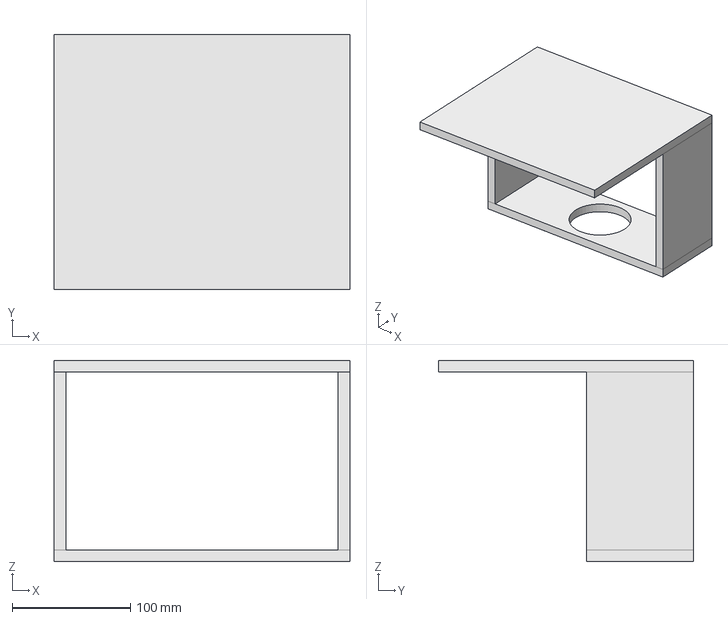
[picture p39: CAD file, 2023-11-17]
Documents/Robot 4T/Assemblage/Arriere.FCStd
250.0 x 215.0 x 170.0 mm

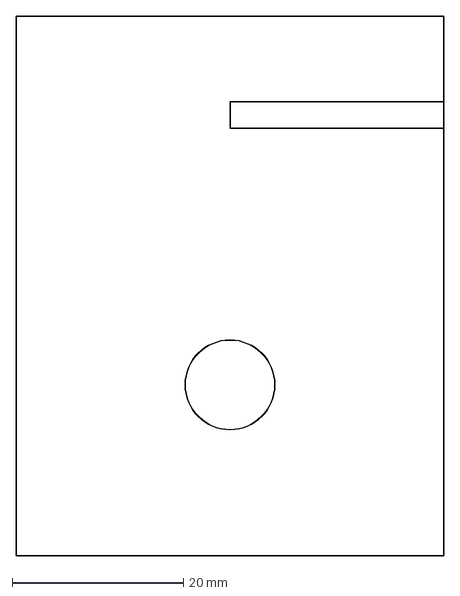
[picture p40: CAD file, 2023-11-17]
Documents/Robot 4T/Decoupage Proto/SupportBras.dxf
50.0 x 63.1 mm

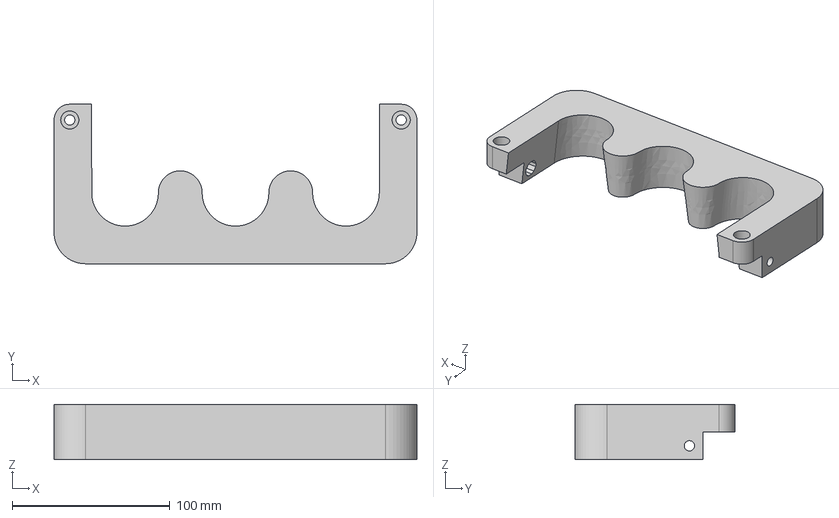
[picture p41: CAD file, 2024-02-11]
Documents/Robot 4T/Griffe Augmenté/Fixe.step
230.0 x 101.1 x 35.0 mm

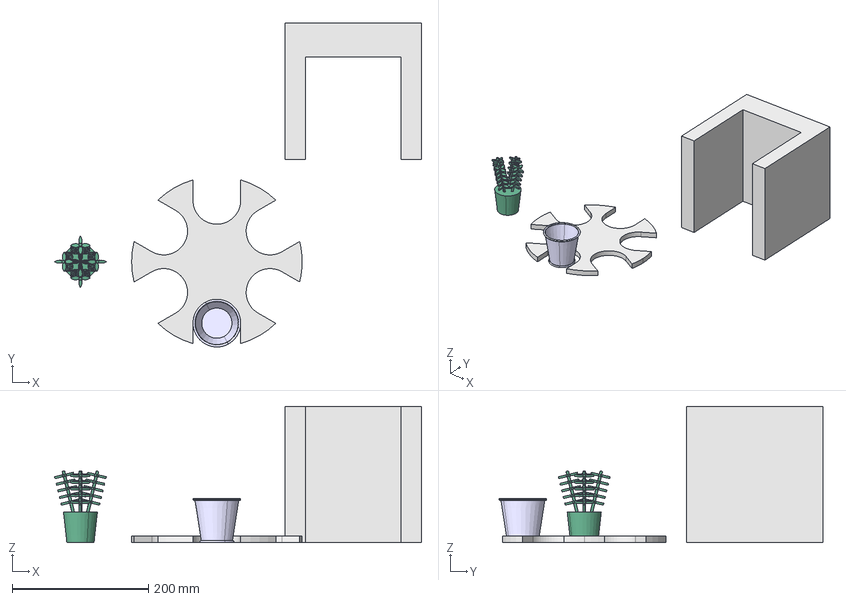
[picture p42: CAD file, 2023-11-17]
Documents/Robot 4T/test.FCStd
538.0 x 475.0 x 200.0 mm
corps001
plante
pot
Plateau

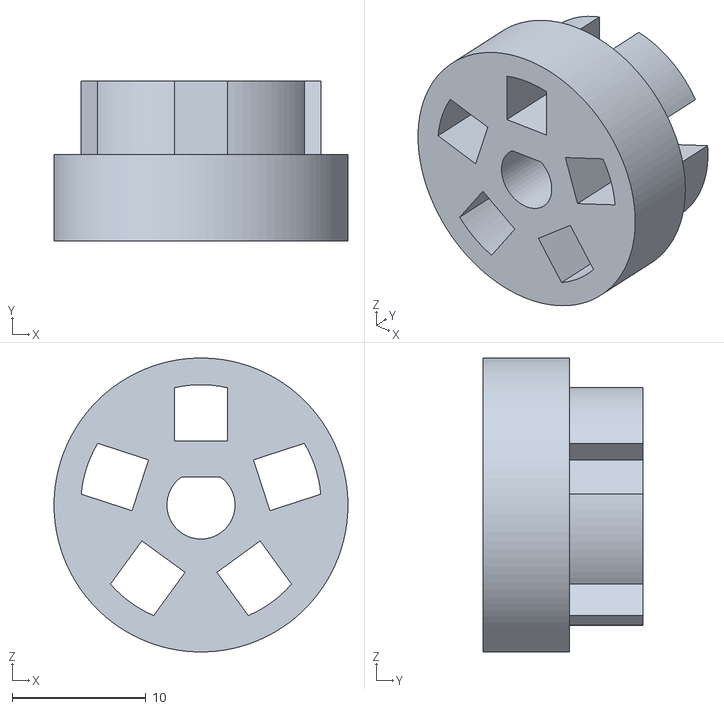
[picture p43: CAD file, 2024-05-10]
Pololu.stl
22.0 x 12.0 x 22.0

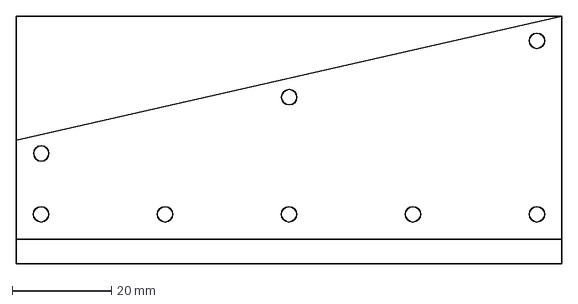
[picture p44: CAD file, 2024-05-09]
Aile.dxf
110.0 x 50.0 mm

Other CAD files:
Decoupe/Base.dxf
Decoupe/Pami/Noeud.dxf
Documents/Fichiers 3D Eurobot/Griffe.obj
Documents/Matériel/3D_FINALE_V1/step/support_balise.stp
Decoupe/Cote.dxf
Decoupe/Pami/Bouche.dxf
Decoupe/Pami/Veste.dxf
Documents/Matériel/3D_2024_BETA/step/Marqueur d_identification.stp
Documents/Matériel/3D_2024_BETA/step/Panneau_solaire.stp
Documents/Matériel/3D_2024_BETA/step/plante.stp
Documents/Matériel/3D_2024_BETA/step/pot.stp
Documents/Matériel/3D_2024_BETA/step/start_tag.stp
Documents/Matériel/3D_2024_BETA/step/support_balise.stp
Documents/Matériel/3D_2024_BETA/step/table_2024.stp
Documents/Matériel/3D_2024_BETA/stl/Panneau_solaire.stl
Documents/Matériel/3D_2024_BETA/stl/plante.stl
Documents/Matériel/3D_2024_BETA/stl/pot.stl
Documents/Matériel/3D_2024_BETA/stl/start_tag.stl
Documents/Matériel/3D_2024_BETA/stl/support_balise.stl
Documents/Matériel/3D_2024_BETA/stl/support_panneau.stl
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

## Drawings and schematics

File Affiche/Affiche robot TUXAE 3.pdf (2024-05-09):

## Robot Principal

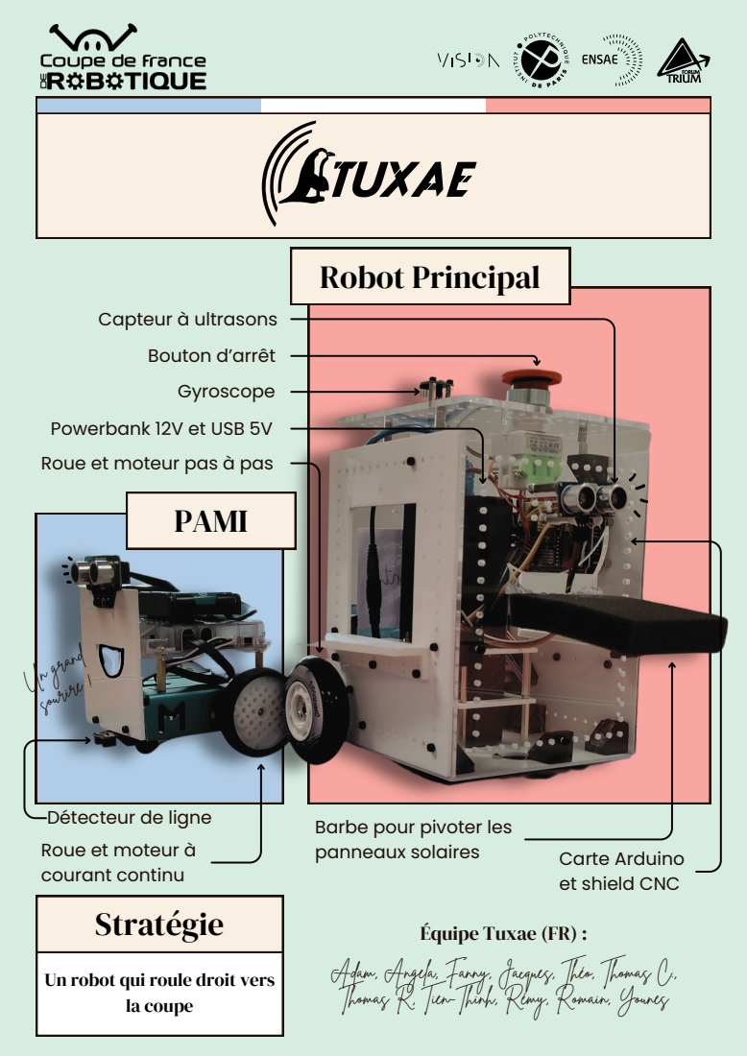
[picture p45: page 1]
PAMI; Gyroscope; Bouton d’arrêt; Un grand sourire !; Capteur à ultrasons; la coupe; Stratégie; Équipe Tuxae (FR) :

Powerbank 12V et USB 5V
Roue et moteur pas à pas

Détecteur de ligne
Roue et moteur à
courant continu

Barbe pour pivoter les
panneaux solaires

Carte Arduino
et shield CNC

Adam, Angela, Fanny, Jacques, Théo, Thomas C.,
Thomas R, Tien-Thinh, Rémy, Romain, Younes

Un robot qui roule droit vers

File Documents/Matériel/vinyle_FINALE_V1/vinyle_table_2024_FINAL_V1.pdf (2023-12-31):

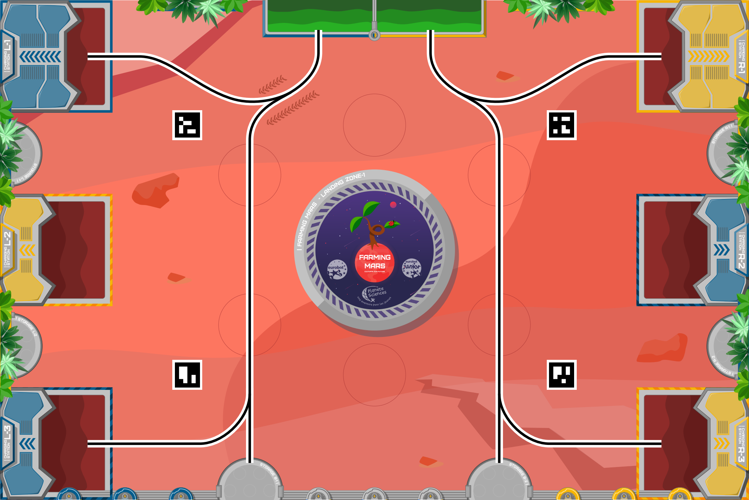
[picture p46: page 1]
| FARMING MARS; LANDING; zone-1; FARMING MARS; | CharGing; | sTation; Storage; Storage B-1 |; Storage B-2 |

sTation L-3 | CharGing | sTation L-2 | CharGing | sTation L-1

CharGing R-3 | sTation | CharGing R-2 | sTATion | CharGing R-1

Cultivate our future

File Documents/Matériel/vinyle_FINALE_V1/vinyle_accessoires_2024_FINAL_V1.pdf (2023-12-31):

## Farming Mars - Aire de jeu officielle 2024

## Farming Mars - Official game area 2024

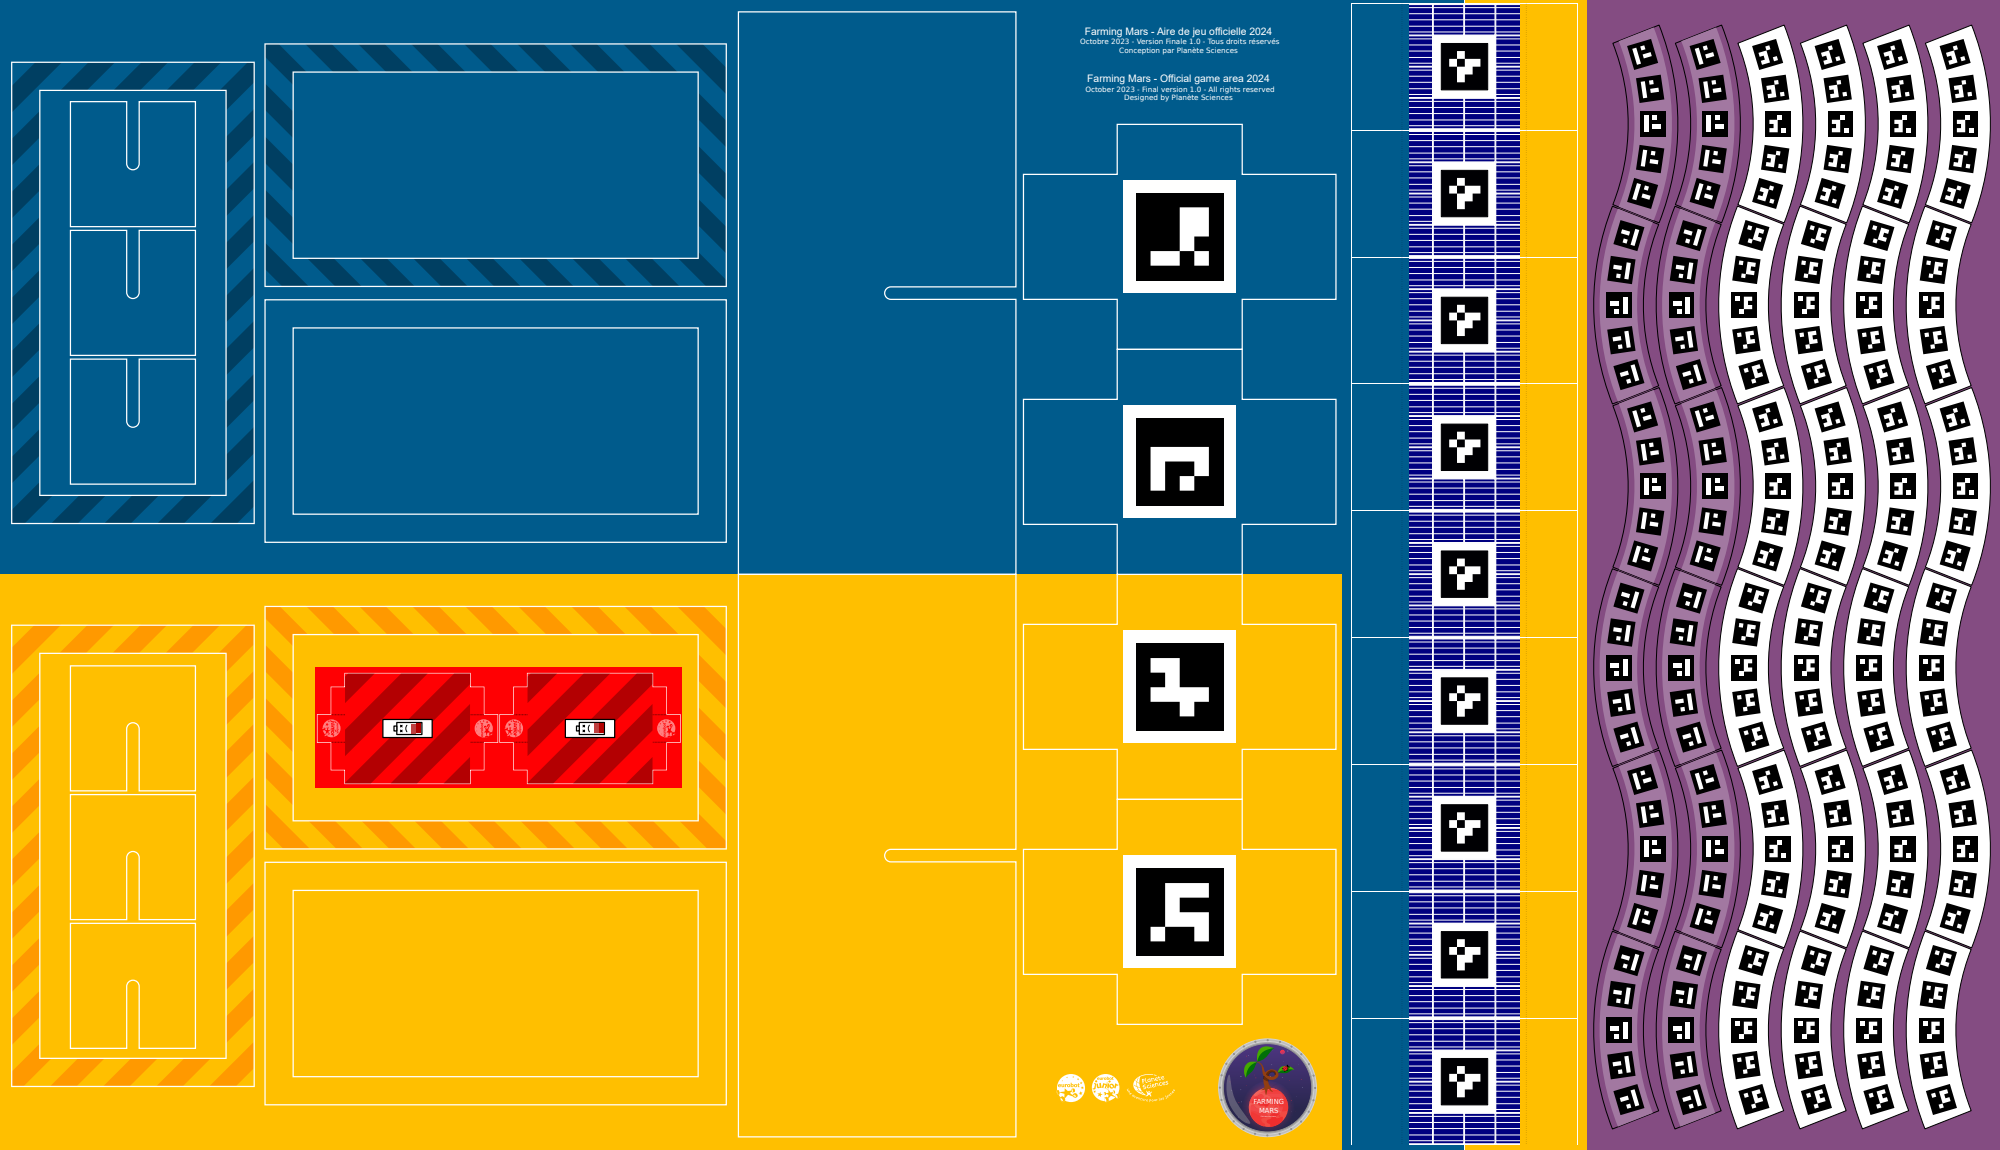
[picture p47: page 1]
FARMING MARS

Octobre 2023 - Version Finale 1.0 - Tous droits réservés

Conception par Planète Sciences

October 2023 - Final version 1.0 - All rights reserved

Designed by Planète Sciences

Cultivate our future

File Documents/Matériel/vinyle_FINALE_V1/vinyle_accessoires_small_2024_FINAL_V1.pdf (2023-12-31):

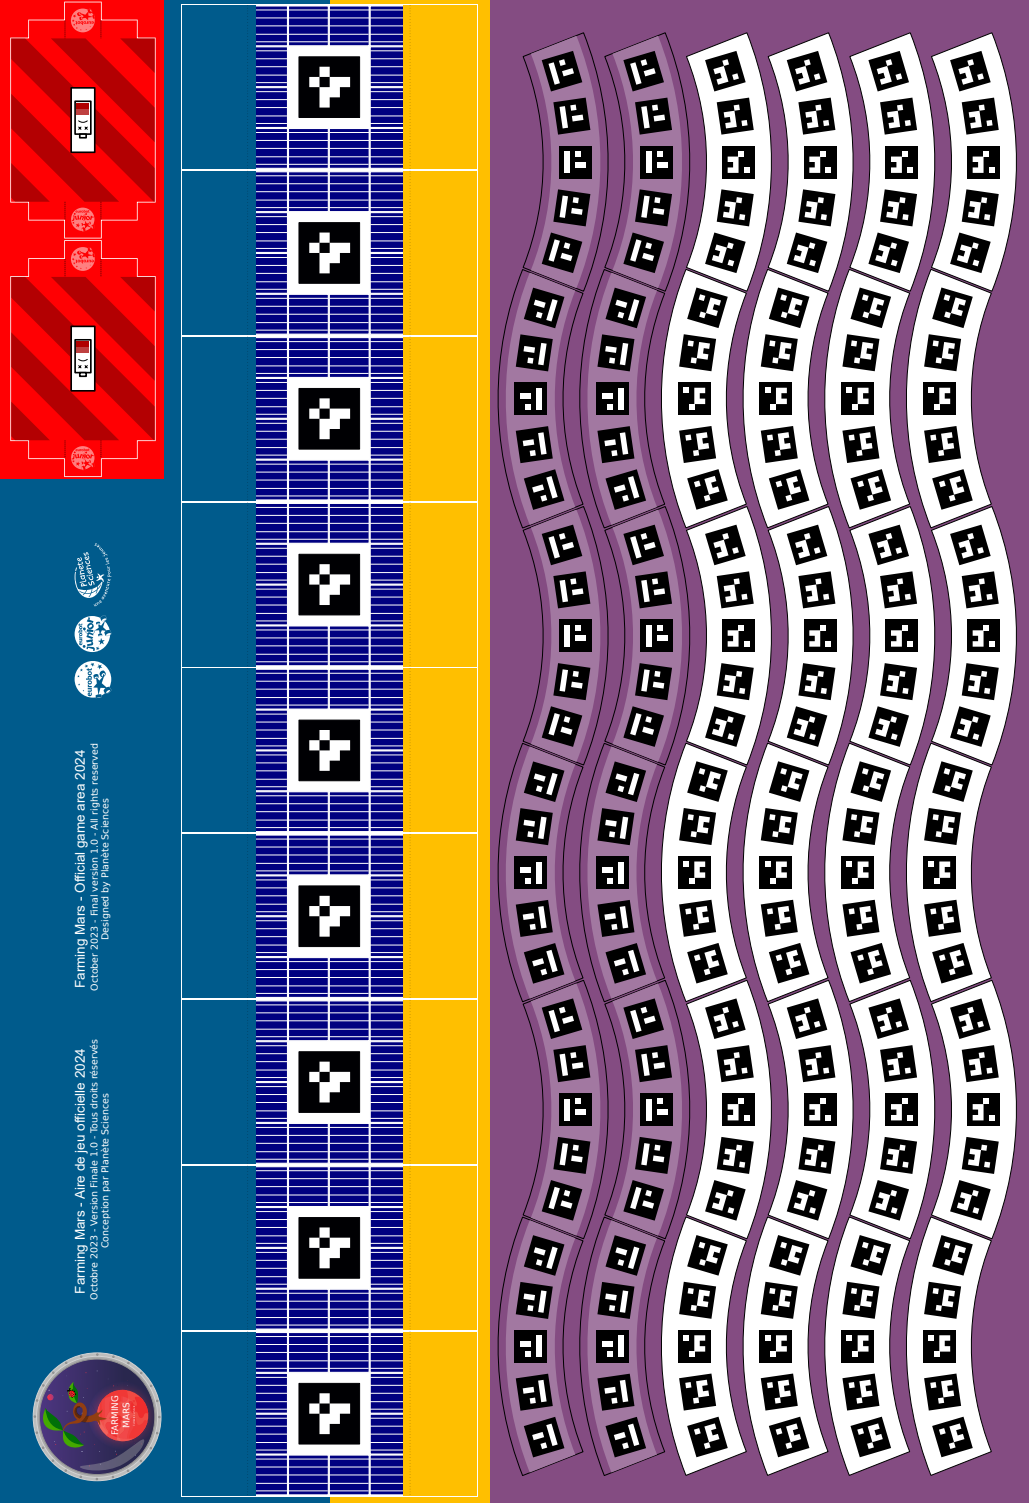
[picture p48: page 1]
FARMING; MARS

October 2023 - Final version 1.0 - All rights reserved

Farming Mars - Official game area 2024

Designed by Planète Sciences

Octobre 2023 - Version Finale 1.0 - Tous droits réservés

Farming Mars - Aire de jeu officielle 2024

Conception par Planète Sciences

Cultivate our future

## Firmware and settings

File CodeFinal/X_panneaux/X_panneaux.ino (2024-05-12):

#include <AccelStepper.h>
#include <Wire.h>
#include <Adafruit_MPU6050.h>
#include <Adafruit_Sensor.h>
#include <math.h> // pour utiliser PI
#include <Arduino.h>
#include <HC_SR04.h>
// AccelStepper https://www.youtube.com/watch?v=QRCvC5xhJCw
// Pour éviter la surchauffe des moteurs Vref https://www.youtube.com/watch?v=BV-ouxhZamI
// Taille de roue 76mm https://www.decathlonpro.fr/paire-roues-oxeloboard-roulements-id-8127600.html

// Mesures
const int roue = 76; // diamètre de la roue en mm
const int essieu = 203; // distance entre les deux roues en mm (vraie distance : 200, mais ajustée pour que le robot tourne du bon angle)
const int xmax = 3000;
const int ymax = 2000;
const int pas_par_tour = 200; // nombre de pas à effectuer pour réaliser un tour

/*
STEP, DIR
X : 2, 5 (Left)
Y: 3, 6 (Right)
Z: 4, 7 (Left)
*/

const int enPin = 8; // enable Pin pour allumer le shield
AccelStepper stepper_L(1, 4, 7);  // 1=using_controller, pull, dir
AccelStepper stepper_R(1, 3, 6);


// Pour les étapes
int etape = 0;
int etape_decalage_panneau = 0;
unsigned long startTime = 0;

// Define Ultrason
#define TRIG_PIN 5
#define ECHO_PIN 2
HC_SR04<ECHO_PIN> sensor(TRIG_PIN);   // sensor with echo and trigger pin
signed long distance;
unsigned long lastUltra = 0;
unsigned long ultraTime = 0;
// unsigned long interval_ultrason;

// Choix équipe
const int readPin = 11; // Z-limit switch
int team = 0;



void setup() {
 	Serial.begin(9600);
  // Allumer le shield
  pinMode(enPin, OUTPUT);
  digitalWrite(enPin, LOW);
  // setup Left
  stepper_L.setMaxSpeed(200.0);
  stepper_L.setAcceleration(200.0);
  // setup Right
  stepper_R.setMaxSpeed(200.0);
  stepper_R.setAcceleration(200.0);

  // Initalize Ultrason
  sensor.beginAsync();  
  sensor.startAsync(100000);        // start first measurement
  ultraTime=millis();
  
  // pinMode(TRIG_PIN, OUTPUT);
  // pinMode(ECHO_PIN, INPUT);
  // interval_ultrason = micros();
  distance = -1;
  // Serial.println(distance);
  // Serial.println("Setup");

  // Choix équipe
  pinMode(readPin, INPUT_PULLUP);
  team = digitalRead(readPin);
}

void loop() {
  ultrason_nonbloquant();
  // Pause execution for 1 second (1000 milliseconds)  
  // Serial.println();
  // Serial.print("Etape : ");
  // Serial.println(etape);
  if (etape==0) {
    // Cache Ultrason
    if (millis() - ultraTime > 3000) {
      if (distance != -1 && distance >10) {
        etape = 1;
        startTime=micros();
      }
    }
  } else if (etape == 1) {  // *** Premiere avance ***
    // Avancer 1.7m soit 1700 mm
    avance(2000);
    etape = 2;
  } else if (etape == 2) {
    // Avancer ok
    if (stepper_L.distanceToGo() == 0 && stepper_R.distanceToGo() == 0 ) {
      etape = 3;
    }
  } else if (etape == 3) {  // *** 2e panneau ***
    // Decalage panneau 2
    decalage_panneau();
    if (etape_decalage_panneau == 0) {
      etape = 4;
    }
  } else if (etape == 4) {   // *** 3e panneau ***
    // Decalage panneau 2
    decalage_panneau();
    if (etape_decalage_panneau == 0) {
      etape = 5;
    }
  } else if (etape == 5) {  // *** Retour Base ***
    // Recule
    avance(-430);
    etape = 6;
  } else if (etape == 6) {
    // Avancer ok
    if (stepper_L.distanceToGo() == 0 && stepper_R.distanceToGo() == 0 ) {
      etape = 7;
    }
  } else if (etape == 7) {
    // Rot 2 Align
    turn(80);
    etape = 8;
  } else if (etape == 8) {
    // Check Rot 2 Align
    if (stepper_L.distanceToGo() == 0 && stepper_R.distanceToGo() == 0 ) {
      etape = 9;
    }
  } else if (etape == 9) {
    // Avancer final
    avance(1000);
    etape = 10;
  } else if (etape == 10) {
    // Check Avancer final
    if (stepper_L.distanceToGo() == 0 && stepper_R.distanceToGo() == 0 ) {
      etape = 11;
    }
  } else if (etape == 100) {
    // Desactivation des moteurs
    digitalWrite(enPin, HIGH);
  } else {
    etape=100;
  }
  
  bool run = true;
  if (distance != -1 && distance < 20) {
    // Serial.println("Obstacle detecté");
    run = false;
  }
  if (startTime != 0) {
    if (micros()-startTime > 95000000) {// 95secondes
      run = false;
      etape = 100;
    }
  }
  // Run motor
  if (run) {
  stepper_L.run();
  stepper_R.run();
  }
}

void decalage_panneau() {
  if (etape_decalage_panneau == 0) {
    etape_decalage_panneau = 1;
  } else if (etape_decalage_panneau == 1) {
    // Recule 1
    avance(-200);
    etape_decalage_panneau = 2;
  } else if (etape_decalage_panneau == 2) {
    // Check recule 1
    if (stepper_L.distanceToGo() == 0 && stepper_R.distanceToGo() == 0 ) {
      etape_decalage_panneau = 3;
    }
  } else if (etape_decalage_panneau == 3) {
    // Rot 1
    turn(60);
    etape_decalage_panneau = 4;
  } else if (etape_decalage_panneau == 4) {
    // Check Rot 1
    if (stepper_L.distanceToGo() == 0 && stepper_R.distanceToGo() == 0 ) {
      etape_decalage_panneau = 5;
    }
  } else if (etape_decalage_panneau == 5) {
    // Recule 2 Diag
    avance(-400);
    etape_decalage_panneau = 6;
  } else if (etape_decalage_panneau == 6) {
    // Check Recule 2 Diag
    if (stepper_L.distanceToGo() == 0 && stepper_R.distanceToGo() == 0 ) {
      etape_decalage_panneau = 7;
    }
  } else if (etape_decalage_panneau == 7) {
    // Rot 2 Align
    turn(-60);
    etape_decalage_panneau = 8;
  } else if (etape_decalage_panneau == 8) {
    // Check Rot 2 Align
    if (stepper_L.distanceToGo() == 0 && stepper_R.distanceToGo() == 0 ) {
      etape_decalage_panneau = 9;
    }
  } else if (etape_decalage_panneau == 9) {
    // Avancer final
    avance(600);
    etape_decalage_panneau = 10;
  } else if (etape_decalage_panneau == 10) {
    // Check Avancer final
    if (stepper_L.distanceToGo() == 0 && stepper_R.distanceToGo() == 0 ) {
      etape_decalage_panneau = 0;
    }
  }
}

void turn(float angle) { // angle est en degre
  // left = +-1, si = +1, alors le moteur gauche recule et le droit avance pour tourner à gauche
  if (team == 0) {
    angle = -angle;
  }
  // Calcul du nombre de pas à effectuer
  long steps = (pas_par_tour * angle*essieu) / (360*roue);
  Serial.println("New turn");
  // Move both stepper motors simultaneously
    stepper_L.moveTo(stepper_L.currentPosition() + steps);
    stepper_R.moveTo(stepper_R.currentPosition() - steps);
}

void avance(float distance) {
  long steps = (pas_par_tour * distance) / (PI*roue);
  Serial.println("New line");
  stepper_L.moveTo(stepper_L.currentPosition() + steps);
  stepper_R.moveTo(stepper_R.currentPosition() + steps);
}

void ultrason() {
  
  long duration;
  // Envoie une impulsion ultrasonique
  digitalWrite(TRIG_PIN, LOW);
  delayMicroseconds(2);
  digitalWrite(TRIG_PIN, HIGH);
  delayMicroseconds(10);
  digitalWrite(TRIG_PIN, LOW);
  
  // Mesure la durée de l'impulsion ultrasonique
  duration = pulseIn(ECHO_PIN, HIGH);
  
  // Convertit la durée en distance (en cm)
  distance = duration * 0.034 / 2;
  if (distance < 2 || distance > 400) {
    distance = -1;
  } 
  
  // Affiche la distance mesurée sur le moniteur série
  Serial.print("Distance: ");
  Serial.print(distance);
  Serial.println(" cm");
}

void ultrason_nonbloquant() {
  if (sensor.isFinished()) {
    if ((micros()-lastUltra) > 100000) {
      // On retire cette valeure
      sensor.getDist_cm();

    } else {distance = sensor.getDist_cm();
      if (distance < 2) {
        distance = -1;
      } 
      if (distance > 400) {
        distance = 400;
      }
      // Serial.print("Distance: ");
      // Serial.print(distance);
      // Serial.println(" cm");
    }
    
  // Serial.print("LastUltra: ");
  // Serial.print((lastUltra - micros())/1000000);
  // Serial.println(" ms");
  lastUltra = micros();
  sensor.startAsync(100000);
  }
}

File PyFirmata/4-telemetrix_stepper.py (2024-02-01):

# https://github.com/MrYsLab/telemetrix/blob/master/examples/stepper_absolute.py
# https://mryslab.github.io/telemetrix/pin_modes/#set_pin_mode_stepper

"""
 Copyright (c) 2022 Alan Yorinks All rights reserved.

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
"""
import sys
import time

from telemetrix import telemetrix

"""
Run a motor to an absolute position. Server will send a callback notification 
when motion is complete.

Motor used to test is a NEMA-17 size - 200 steps/rev, 12V 350mA.
And the driver is a TB6600 4A 9-42V Nema 17 Stepper Motor Driver.

The driver was connected as follows:
VCC 12 VDC
GND Power supply ground
ENA- Not connected
ENA+ Not connected
DIR- GND
DIR+ GPIO Pin 23 ESP32
PUL- ESP32 GND
PUL+ GPIO Pin 22 ESP32
A-, A+ Coil 1 stepper motor
B-, B+ Coil 2 stepper motor

"""

# GPIO Pins
PULSE_PIN = 8
DIRECTION_PIN = 9

# flag to keep track of the number of times the callback
# was called. When == 2, exit program
exit_flag = 0


def the_callback(data):
    global exit_flag
    date = time.strftime('%Y-%m-%d %H:%M:%S', time.localtime(data[2]))
    print(f'Motor {data[1]} absolute motion completed at: {date}.')
    exit_flag += 1


def running_callback(data):
    if data[1]:
        print('The motor is running.')
    else:
        print('The motor IS NOT running.')


def step_absolute(the_board):   

    global exit_flag
    # create an accelstepper instance for a TB6600 motor drive
    # if you are using a micro stepper controller board:
    # pin1 = pulse pin, pin2 = direction
    # motor = the_board.set_pin_mode_stepper(interface=1, pin1=PULSE_PIN, pin2=DIRECTION_PIN)

    # if you are using a 28BYJ-48 Stepper Motor with ULN2003
    # comment out the line above and uncomment out the line below.
    motor = the_board.set_pin_mode_stepper(interface=4, pin1=8, pin2=9, pin3=10, pin4=11)

    # the_board.stepper_is_running(motor, callback=running_callback)
    time.sleep(.5)

    # set the max speed and acceleration
    the_board.stepper_set_current_position(0, 0)
    the_board.stepper_set_max_speed(motor, 400)
    the_board.stepper_set_acceleration(motor, 800)

    # set the absolute position in steps
    the_board.stepper_move_to(motor, 2000)

    # run the motor
    print('Starting motor...')
    the_board.stepper_run(motor, completion_callback=the_callback)
    time.sleep(.2)
    the_board.stepper_is_running(motor, callback=running_callback)
    time.sleep(.2)
    while exit_flag == 0:
        time.sleep(.2)

    the_board.stepper_set_current_position(0, 0)
    the_board.stepper_set_max_speed(motor, 400)
    the_board.stepper_set_acceleration(motor, 800)
    # set the absolute position in steps
    print('Running motor in opposite direction')
    the_board.stepper_move_to(motor, -2000)

    the_board.stepper_run(motor, completion_callback=the_callback)
    time.sleep(.2)
    the_board.stepper_is_running(motor, callback=running_callback)
    time.sleep(.2)

    # keep application running
    while exit_flag < 2:
        try:
            time.sleep(.2)
        except KeyboardInterrupt:
            the_board.shutdown()
            sys.exit(0)
    the_board.shutdown()
    sys.exit(0)


# instantiate telemetrix
board = telemetrix.Telemetrix()
try:
    # start the main function
    step_absolute(board)
    board.shutdown()
except KeyboardInterrupt:
    board.shutdown()
    sys.exit(0)

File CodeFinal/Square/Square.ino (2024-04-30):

#include <AccelStepper.h>
#include <Wire.h>
#include <Adafruit_MPU6050.h>
#include <Adafruit_Sensor.h>
#include <math.h> // pour utiliser PI
// AccelStepper https://www.youtube.com/watch?v=QRCvC5xhJCw
// Pour éviter la surchauffe des moteurs Vref https://www.youtube.com/watch?v=BV-ouxhZamI
// Taille de roue 76mm https://www.decathlonpro.fr/paire-roues-oxeloboard-roulements-id-8127600.html

// Mesures
const int roue = 76; // diamètre de la roue en mm
const int essieu = 203; // distance entre les deux roues en mm (vraie distance : 200, mais ajustée pour que le robot tourne du bon angle)
const int xmax = 3000;
const int ymax = 2000;
const int pas_par_tour = 200; // nombre de pas à effectuer pour réaliser un tour

bool line = true;

/*
STEP, DIR
X : 2, 5 (Left)
Y: 3, 6 (Right)
Z: 4, 7
*/

const int enPin = 8; // enable Pin pour allumer le shield
AccelStepper stepper_L(1, 2, 5);  // 1=using_controller, pull, dir
AccelStepper stepper_R(1, 3, 6);

// Pour le gyroscope
unsigned long previousMicros = 0; // Temps du dernier update rotation
float mean_err_gz = 0.0;
float angle_gyro = 0.0;

// Initialisation de l'objet MPU6050
Adafruit_MPU6050 mpu;



void setup() {
 	Serial.begin(9600);
  // Allumer le shield
  pinMode(enPin, OUTPUT);
  digitalWrite(enPin, LOW);
  // setup Left
  stepper_L.setMaxSpeed(600.0);
  stepper_L.setAcceleration(400.0);
  // setup Right
  stepper_R.setMaxSpeed(600.0);
  stepper_R.setAcceleration(400.0);

  // Initalize serial monitor
  Serial.begin(115200);
  while (!Serial) {
    delay(10);
  }

  // Try to initialize gyroscope
  if (!mpu.begin()) {
    Serial.println("Failed to find MPU6050 chip");
    while (1) {
      delay(10);
    }
  }
  mpu.setAccelerometerRange(MPU6050_RANGE_4_G);
  mpu.setGyroRange(MPU6050_RANGE_250_DEG);
  mpu.setFilterBandwidth(MPU6050_BAND_21_HZ);
  Serial.println("");
  delay(100);

  Serial.println("Gyro initialisé");
}

void loop() {
  // Pause execution for 1 second (1000 milliseconds)  
  if (stepper_L.distanceToGo() == 0 && stepper_R.distanceToGo() == 0 ) {
    delay(1000);
    if (line) {
    Serial.println("new line");
    stepper_L.moveTo(stepper_L.currentPosition() + 800);
    stepper_R.moveTo(stepper_R.currentPosition() + 800);
    line = false;

    } else {
    //compute_error_gyro(); // peut-être à mettre dans la void setup
    turn(PI/2);
    angle_gyro = 0.0;
    line = true;

    }

  }


  // Run motor
  if (line) {
    unsigned long currentMicros = micros();
    float DT = (currentMicros-previousMicros) / 1000000;
    // Exécute la tâche de rotation toutes les DT secondes
    if (DT >= 0.01) {
      compute_angle_gyro(DT);
      //correct_angle(PI/2);
      previousMicros = currentMicros;
  }
}
  stepper_L.run();
  stepper_R.run();

}



void turn(float angle) { 
  // left = +-1, si = +1, alors le moteur gauche recule et le droit avance pour tourner à gauche

  // Calcul du nombre de pas à effectuer
  long steps = (pas_par_tour * angle*essieu) / (2*PI*roue);
  Serial.println("New turn");
  Serial.println(stepper_L.currentPosition());
  Serial.println(stepper_R.currentPosition());
  // Move both stepper motors simultaneously
    stepper_L.moveTo(stepper_L.currentPosition() + steps);
    stepper_R.moveTo(stepper_R.currentPosition() - steps);
}

void compute_error_gyro(){
  float sum_err_gz = 0.0;
  const int n = 1000;
  for (int i = 0; i < n; i++) {
    // Lecture des données du gyroscope
    sensors_event_t a, g, temp;
    mpu.getEvent(&a, &g, &temp);
    // Calcul de la vitesse de rotation (en radian/s)
    float err_gz = g.gyro.z;
    sum_err_gz += err_gz;
    delay(1);
  }
  // Calcul de la moyenne
  mean_err_gz = sum_err_gz / n;
}


void compute_angle_gyro(float DT) {
  // Lecture des données du gyroscope
  sensors_event_t a, g, temp;
  mpu.getEvent(&a, &g, &temp);

  // Lecture des données de rotation (en rad/s)
  float gz = g.gyro.z;
  angle_gyro += (gz-mean_err_gz) * DT; // Mise à jour de la rotation

  // Affichage de la rotation en degrés
  Serial.print("vitesse : ");
  Serial.print(gz);
  Serial.print("rad/s ; angle : ");
  Serial.println(angle_gyro * 180 / M_PI);

}

void correct_angle(float angle) {
  float err_angle = (angle * 180 / M_PI) - angle_gyro;
  if (abs(err_angle) > 10) {
    turn(err_angle);
  }

}

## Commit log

2023-11-17 rendu privé
    [Arriere.FCStd, Assemblage.FCStd, AxeBras.dxf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]
2023-11-25 Implémentation de get_position
    Je vais faire une petite feuille pour expliquer les maths.
2023-12-31 Nouveaux documents
    [Marqueur d_identification.stp, Panneau Solaire.stp, Pot_Plante.stl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]
2024-01-04 Spec recherches stepper motor et batterie
2024-01-30 pyfirmata stepper motor
2024-01-31 telemetrix stepper motor ok
2024-02-06 Add files via upload
    Première implémentation simple du filtre de Kalman extensif à partir du site https://automaticaddison.com/extended-kalman-filter-ekf-with-python-code-example/
2024-02-06 Update README.md
    Rajout de documentations sur le filtre de Kalman
2024-02-06 Add files via upload
    Cours filtre de Kalman ENSTA
2024-02-12 gyro calculs
2024-02-12 réorg et correction rotation
    [BaseDiff.py, Trajectoire.py, main_avec_gyro.py]
2024-02-19 gyro calibration et calcul position (arduino)
2024-02-19 correction de la rotation
    [BaseDiff.py, Trajectoire.py, main_avec_gyro.py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]
2024-02-22 calcul avec des moyennes
2024-02-22 moyenne de valeurs
2024-02-25 Add files via upload
    Adaptation mineure du code du filtre de Kalman (3 composantes du vecteur de contrôle u = (vx,vy,omega) et test sur ligne droite et tour de plateau
2024-04-29 gyroscope et millis pour rotation
2024-04-29 correction angle de rotation avec gyro
    [Square.ino]
2024-04-30 Gyro correct angle
2025-05-16 Update code Robot
    Ajout des paramétrages des différents chemins faits par le robot durant la précoupe 2025
2025-05-16 Update code pamis
    Ajout du code des différents pamis et organisation des dossiers

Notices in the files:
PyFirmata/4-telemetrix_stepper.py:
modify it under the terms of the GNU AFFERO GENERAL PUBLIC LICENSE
